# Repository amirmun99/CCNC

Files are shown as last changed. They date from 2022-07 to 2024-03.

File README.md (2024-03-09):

# The CCNC
A Cheap (Relatively), yet capable CNC router/mill
<br> 
-----
Cheaper_CNC_Master_Build_Threaded_2022-Jul-21_03-48-01AM-000_CustomizedView20607925930
Cheaper_CNC_Master_Build_Threaded_2022-Jul-15_05-47-59AM-000_CustomizedView9717156544
Cheaper_CNC_Master_Build_Threaded_2022-Jul-15_05-22-21AM-000_CustomizedView19849931560

The Goal for this project is to create a relatively cheap (Sub $500CAD) CNC Machine that is capable of cutting wood, plastics and soft metals. 

This machine utilizes many 3D Printed parts in order to keep costs down, assuming you already have a 3D Printer. Some printed parts have off the shelf alternatives, some can also be replicated in wood using basic hand tools, while other (Mainly the X Gantry Uprights) have to be printed. More information is found in the documents.

The machine/files should be relatively adapatble to different use cases

This assembly guide is rough, but will be refined and updated as the design gets better overall

# Parts (bill of materials)

The Bill of Materials is available in multiple versions
PDF
Spreadsheet
Markdown

There are a few tools that are required to put this machine together;

* Metric Hex/Allen Keys
* Jigsaw with metal cutting blades/Chop saw (Essentially some way to cut the aluminum extrusions and leadscrews)
* M5 Tap Drill
* Circular Saw (To cut the MDF Spoilboard)
* Drill bit set

# Prepare Raw Materials

#### 1. Print and Prepare required parts
Follow the Print Settings file in the STLs Folder

#### 2. Cut Aluminum Extrusions
Follow the Cutlist file, I would recomend not cutting the X Axis extrusions until the uprights are mounted in order to get a snug fit. 

#### 3. Tap Aluminum Extrusions
All of the extrusions need to be threaded with an M5x0.50 tap, except for the 2 frame crossmembers.

#### 4. Cut Lead Screws
Follow the cutlist file if you need to cut your leadscrews, if you purchase the legnths I listed in the parts list, there is no cutting required

# Build the Machine

## 1. Assemble the frame

#### 1. Mounting the Extrusions
Start by mounting a pair of 520mm extrusions to each pair of brackets as shown in the photo (Using M5x20 SHCS). Then attach the 450mm Crossmembers using the corner brackets.
Cheaper_CNC_Master_Build_Threaded_2022-Jul-27_03-12-39PM-000_CustomizedView15145977333 (2)

#### 2. Mount the Linear Rails
Mount the 500mm Linear rails on top of the top most frame rail using M3x8 SHCS as well as M3 T-Nuts. Leave 10mm of gap on either side of the rail.
Cheaper_CNC_Master_Build_Threaded_2022-Jul-27_03-23-58PM-000_CustomizedView48378132536 (2)

#### 3. Mount the Pillow Blocks and hard stops
Mount one pillow block to each of the front frame brackets using M5x16 SHCS. Use the top screw to also mount the Y Axis hard stop. I would recommend tapping these holes as well.
Cheaper_CNC_Master_Build_Threaded_v2_2022-Aug-07_02-21-52AM-000_CustomizedView17407069426

#### 4. Mount Stepper motors 
Prepare 2 stepper motors by installing a flexible coupler onto each, then mount one to each of the rear frame brackets using M3x55 SHCS and the 3D Printed Spacers.
Cheaper_CNC_Master_Build_Threaded_v2_2022-Aug-07_02-25-20AM-000_CustomizedView8771721841

#### Frame is Assembled
Ensure frame is square by utilizing a carpenters square and that all bolts are tight.

## 2. Assemble the X Axis Gantry

#### 1. Prepare the Uprights
Install T-Flanges into the X Gantry Uprights

#### 2. Mount Uprights to Frame
Using 16 M3x18 SHCS, mount both uprights to to the frame as shown in the photo. 
[Cheaper_CNC_Master_Build_Threaded_v2_2022-Aug-07_02-33-53AM-000_CustomizedView3710265809](https://user-images.githubusercontent.com/37276609/183272637-f534e99f-406f-4ec1-a07f-7fb0adbf4d35.png)

#### 3. Install X Axis Extrusion and Rails
Using 4 M5x20 SHCS, Mount both 530mm extrusions to the uprights. The small flanges should help the extrusions stay square during assembly. 
Cheaper_CNC_Master_Build_Threaded_v2_2022-Aug-07_02-40-22AM-000_CustomizedView10348442718

#### 4. Install X Axis Stepper Motor
Prepare the stepper motor by installing a flexible coupler onto the shaft, then mount to the right side upright using M3x55 SHCS and the 3D Printed Spacers.
Cheaper_CNC_Master_Build_Threaded_v2_2022-Aug-07_02-43-08AM-000_CustomizedView12554706739

## 3. Assemble Z Axis Gantry

#### 1. Mount the Linear Rails

#### 2. Mount the Motor

#### 3. Attach Z Axis to X Axis

#### 4. Attach Spindle Mounting Plate

#### 5. Install Lead Screw

#### 6. Install Spindle Mount

## 4. Install Lead Screws and Wiring

## 5. Wire up the Machine

----
Yes, these instructions aren't great. I am planning on releasing a much more detailed video tutorial once V2 is finalized. I am still constantly iterating and upgrading this machine and don't want to create a detailed guide only for it to be outdated within days.

----

### License
<br />This work is licensed under a <a rel="license" href="http://creativecommons.org/licenses/by-nc/4.0/">Creative Commons Attribution-NonCommercial 4.0 International License</a>.

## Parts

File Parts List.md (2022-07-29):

| Category | Part | Quantity | Link |
| --- | --- | --- | ---- |
| Motion | Nema 17 Stepper Motor | 4 |
| | 500mm Linear Rails | 4 | [Amazon](https://www.amazon.ca/gp/product/B08T6WYYVK/ref=ppx_yo_dt_b_asin_title_o00_s00?ie=UTF8&th=1)
| | 200mm Linear Rails | 2 | [Amazon](https://www.amazon.ca/gp/product/B08T6WYYVK/ref=ppx_yo_dt_b_asin_title_o00_s00?ie=UTF8&th=1)
| | 600mm T8x2 Lead Screws | 3 | [Amazon](https://www.amazon.ca/gp/product/B08Y1KNH1B/ref=ppx_yo_dt_b_asin_title_o09_s00?ie=UTF8&psc=1)
| | 200mm T8x2 Lead Screw | 1 | [Amazon](https://www.amazon.ca/200mm%EF%BC%887-88-Inches%EF%BC%89Tr8x2-Thread-Printer-Machine/dp/B08JLGMSML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)
| | Linear Rail Blocks | 8 | [Amazon](https://www.amazon.ca/gp/product/B08T6WYYVK/ref=ppx_yo_dt_b_asin_title_o00_s00?ie=UTF8&th=1)
| | T8 Flange Nuts | 4 |
| | Stepper Motor Couplers 5x8mm | 4 | [Amazon](https://www.amazon.ca/gp/product/B07JL1QYLS/ref=ppx_yo_dt_b_asin_title_o01_s00?ie=UTF8&psc=1)
| | 8mm Pillow Blocks | 2 | 
| | | |
| Frame | 450mm 2020 Extrusion | 2 | [Amazon](https://www.amazon.ca/gp/product/B09PY978PD/ref=ppx_yo_dt_b_asin_title_o02_s01?ie=UTF8&psc=1)
| | 520mm 2020 Extrusion | 4 | [Amazon](https://www.amazon.ca/gp/product/B09PY978PD/ref=ppx_yo_dt_b_asin_title_o02_s01?ie=UTF8&psc=1)
| | 530mm 2020 Extrusion | 2 | [Amazon](https://www.amazon.ca/gp/product/B09PY978PD/ref=ppx_yo_dt_b_asin_title_o02_s01?ie=UTF8&psc=1)
| | 90 Degree Extrusion Brackets | 4 | [Amazon](https://www.amazon.ca/Aluminum-Bracket-L-Shape-Extrusion-2020-20PCS/dp/B09TR3NR8V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)
| | | |
| Fasteners | M3x8 Socket Head Screw | 100 |
| | M3x18 Socket Head Screw | 50 |
| | M3x55 Socket Head Screw | 20 |
| | M3x50 Socket Head Screw | 10 |
| | M5x20 Socket Head Screw | 10 |
| | M5x16 Socket Head Screw | 10 |
| | M2.5x8 Button Head Screw | 10 |
| | M3 T Nuts | 80 |
| | M3 Flat Washers | 50 |
| | | |
| Printed Parts | Front Bracket | 2 |
| | Rear Bracket | 2 |
| | Right X Gantry | 1 |
| | Left X Gantry | 1 |
| | Z Carriage | 1 |
| | Z Platform | 1 |
| | Spindle Mount | 1 |
| | Motor Spacers | 16 |

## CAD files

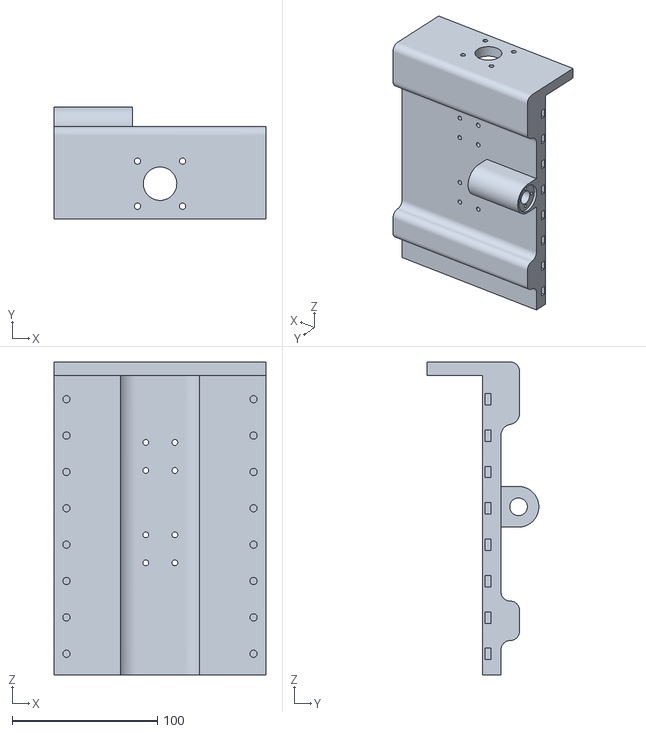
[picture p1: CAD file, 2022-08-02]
STLs/Z Gantry v2.stl
145.7 x 76.8 x 215.2

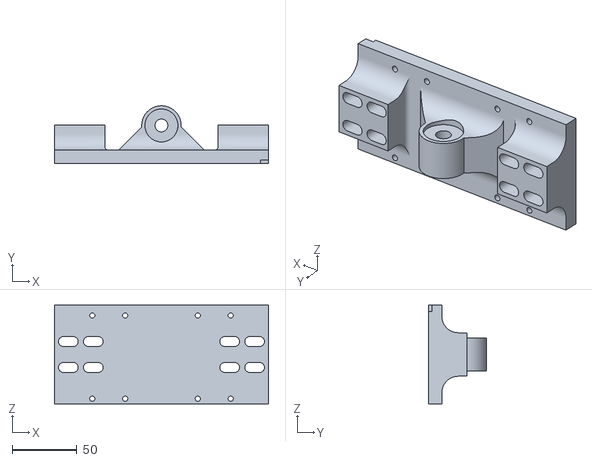
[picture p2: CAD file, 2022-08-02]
STLs/Tool Mount v2.stl
165.1 x 44.4 x 76.2

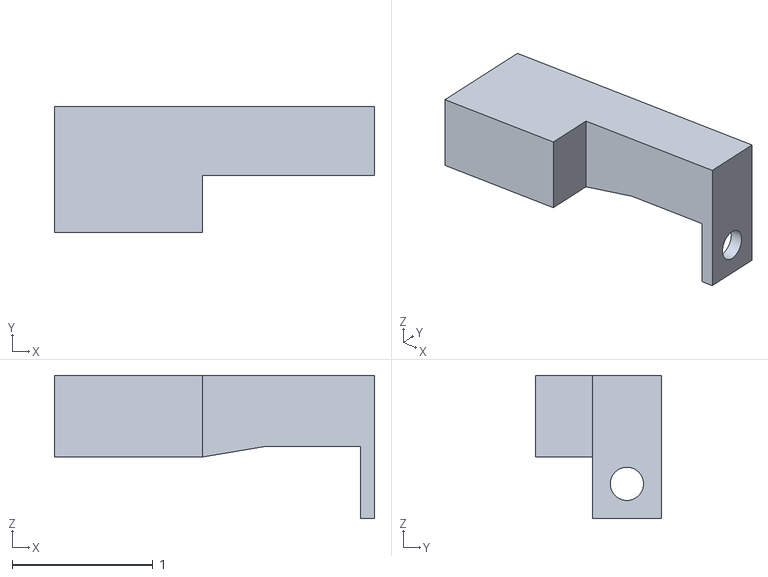
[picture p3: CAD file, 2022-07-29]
STLs/Left Front Stop Block.stl
2.28 x 0.9 x 1.02

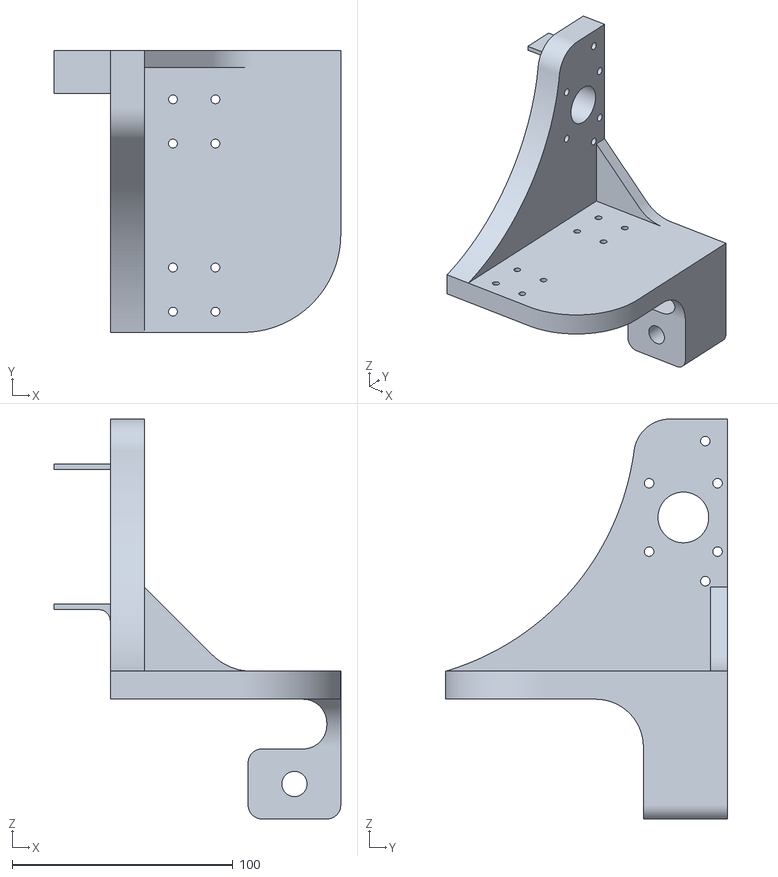
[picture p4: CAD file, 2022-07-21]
STLs/Right X Gantry Upright v2.stl
129.9 x 127.7 x 181.3

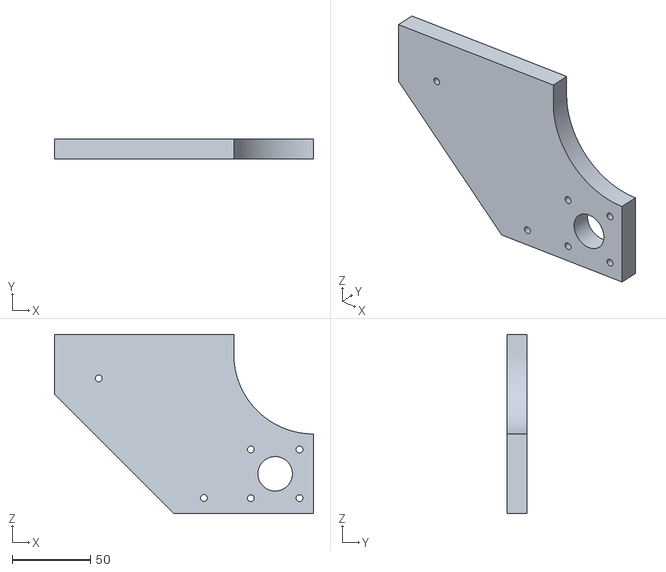
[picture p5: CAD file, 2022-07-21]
STLs/Rear Frame Bracket.stl
165.1 x 12.7 x 114.3

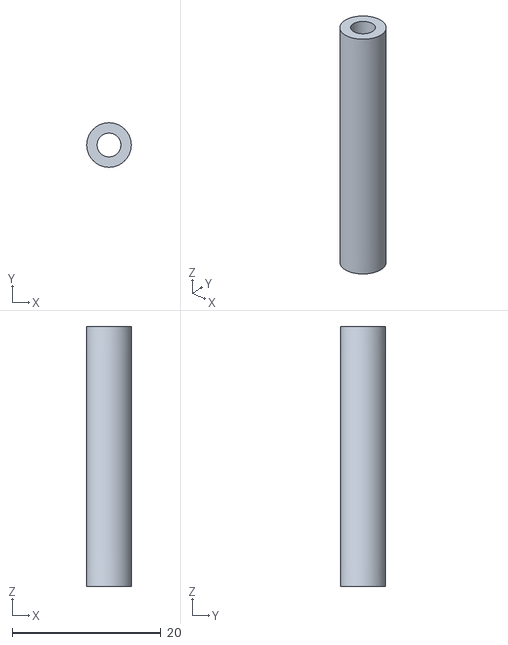
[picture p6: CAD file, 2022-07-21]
STLs/Motor Spacers.stl
6.00 x 6.00 x 35.0

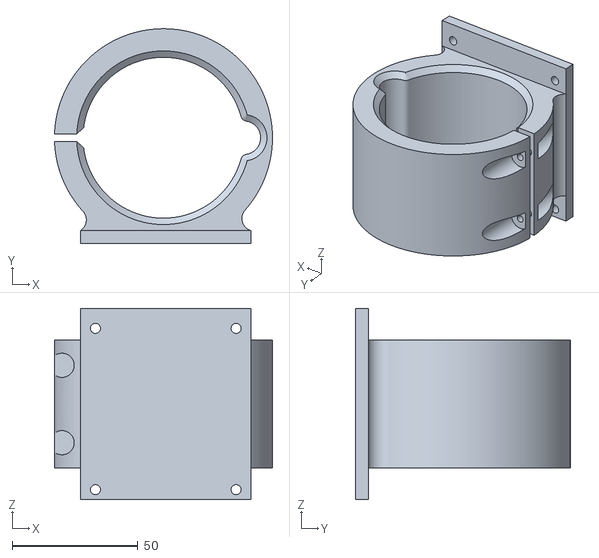
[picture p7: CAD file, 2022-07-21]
STLs/Spindle Mount.stl
86.8 x 85.4 x 76.2

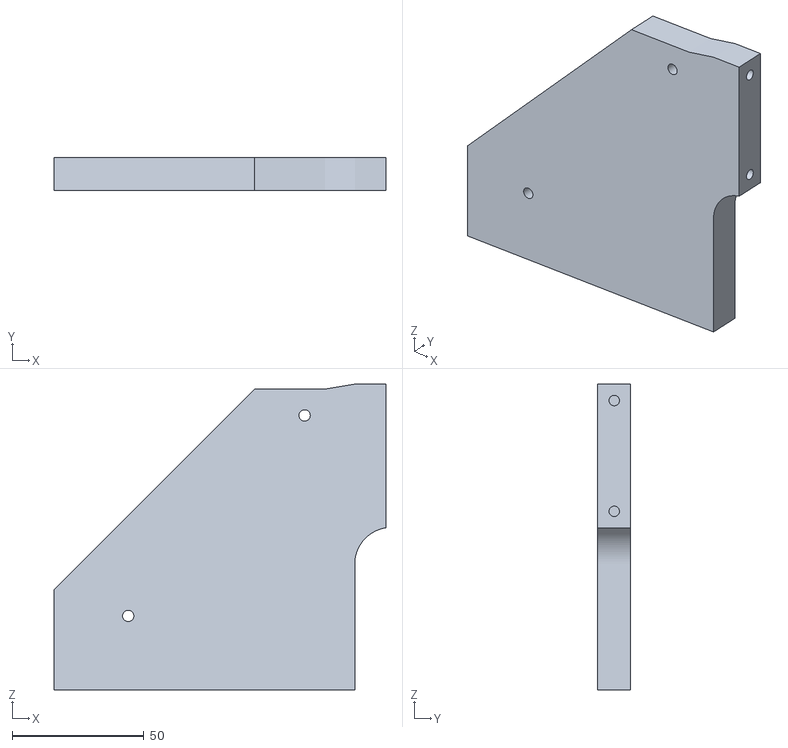
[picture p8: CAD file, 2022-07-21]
STLs/Front Frame Bracket.stl
126.2 x 12.7 x 116.2

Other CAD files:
STLs/Right Front Stop Block.stl
STLs/Left X Gantry Upright v2.stl

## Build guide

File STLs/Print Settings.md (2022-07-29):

Below are the settings that I used to print the initial CCNC. These settings are likely overkill in terms of strength.

My entire machine is printed with normal Polymaker PLA, inclduing the components near the spindle. I would recommend printing these in PETG to add heat resistance.

| **File** | **Walls** | **Infill** | **Recommended Material** | **Support** |
|---|---|---|---|---|
| Front Frame Bracket | 3 | 30 | PLA | No
| Rear Frame Bracket |  3 | 30 | PLA | No
| Left X Gantry Upright  | 4 | 20 | PLA | Yes, Touching Buildplate
| Right X Gantry Upright | 4 | 20 | PLA | Yes, Touching Buildplate
| Z Gantry | 4 | 45 | PETG | Yes, touching Buildplate
| Tool Mount | 4 | 30 | PETG | No
| Makita Router Mount | 4 | 50 | PETG | No
| Motor Spacers | 2 | 100 | PLA | No
| Left Front Stop Block  | 3 | 50 | PLA | No
| Right Front Stop Block | 3 | 50 | PLA | No

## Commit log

2022-07-21 Create Print Settings.md
2022-07-21 Update Print Settings.md
